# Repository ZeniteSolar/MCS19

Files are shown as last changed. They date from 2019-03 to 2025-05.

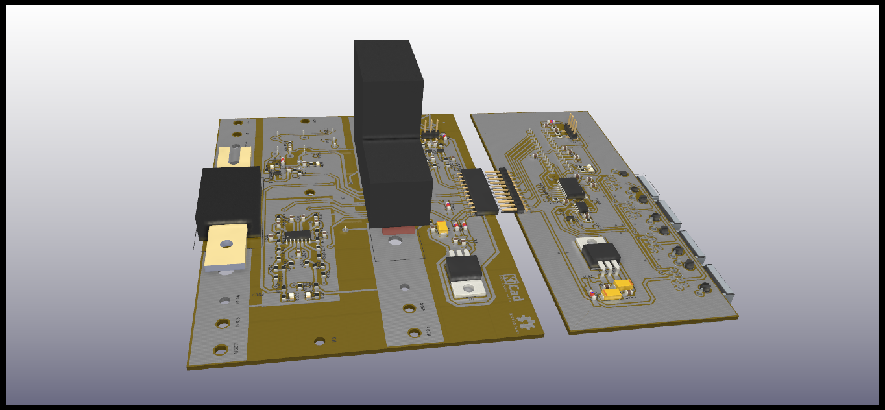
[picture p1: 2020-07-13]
hardware/IMG/3DUP.png

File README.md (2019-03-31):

# MCS19
**M**ódulo de **C**arregamento do **S**istema 2019  
Embarcação Guarapuvu II  
Equipe Zênite Solar  

### Sobre

Este módulo é responsável por gerenciar o carregamento do sistema com a finalidade de garantir segurança para a embarcação.

#### Requisitos e Abordagens
1. Gerenciar a conexão elétrica entre as baterias e o restante do sistema.
    - Utilizar de um relé de alta potência.
    - Ser controlado através da rede CAN da embarcação.
2. Proteger o sistema de falhas por sobre-corrente.
    - Utilizar de um fusível corretamente dimensionado.
3. Realizar o carregamento do banco de capacitores de maneira segura.
    - Utilização de um circuito de inrush.
        - Utilizar de um NTC para limitar o di/dt.
        - Utilizar de um resistor para limitar o pico de corrente
        - Utilizar de um relé para garantir a desconexão completa entre o sistema
      e o banco de baterias.
4. Facilitar o diagnóstico
    - Utilizar reportagens pela rede CAN
    - Utilizar LEDs e Buzzer
        - Sinalizar o estado dos relés
            - Relé do inrush
            - Relé principal
        - Sinalizar o estado do fusível principal
5. Garantir fixação mecânica que não flexione a PCB
    - Utilizar estrutura auxiliar de material isolante

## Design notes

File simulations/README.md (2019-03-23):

# Simulations
Software: LTSPICE

Arquivo: system_inrush.asc  
Descrição: simulação para validar considerando a topologia geral do sistema

Arquivo: ntc_inrush_temp_and_tol_variation.asc  
Descrição: simulação para validar o ntc considerando as tolerância e difernetes
temperaturas ambiente.

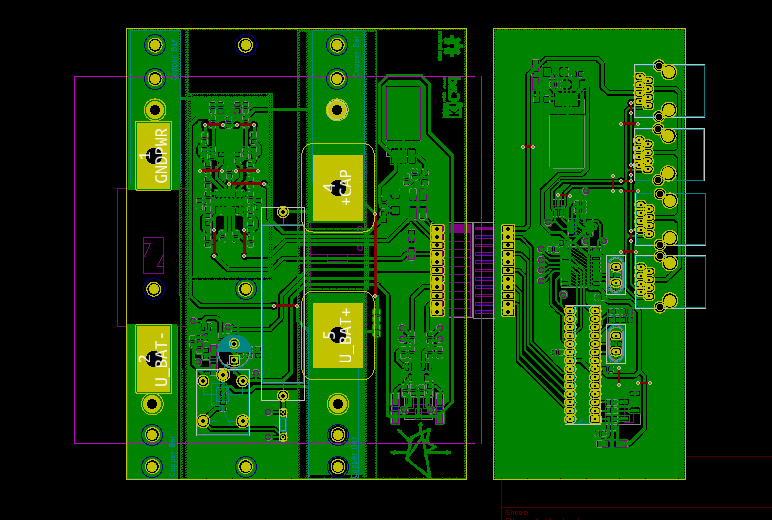
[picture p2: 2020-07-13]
hardware/IMG/layout.png

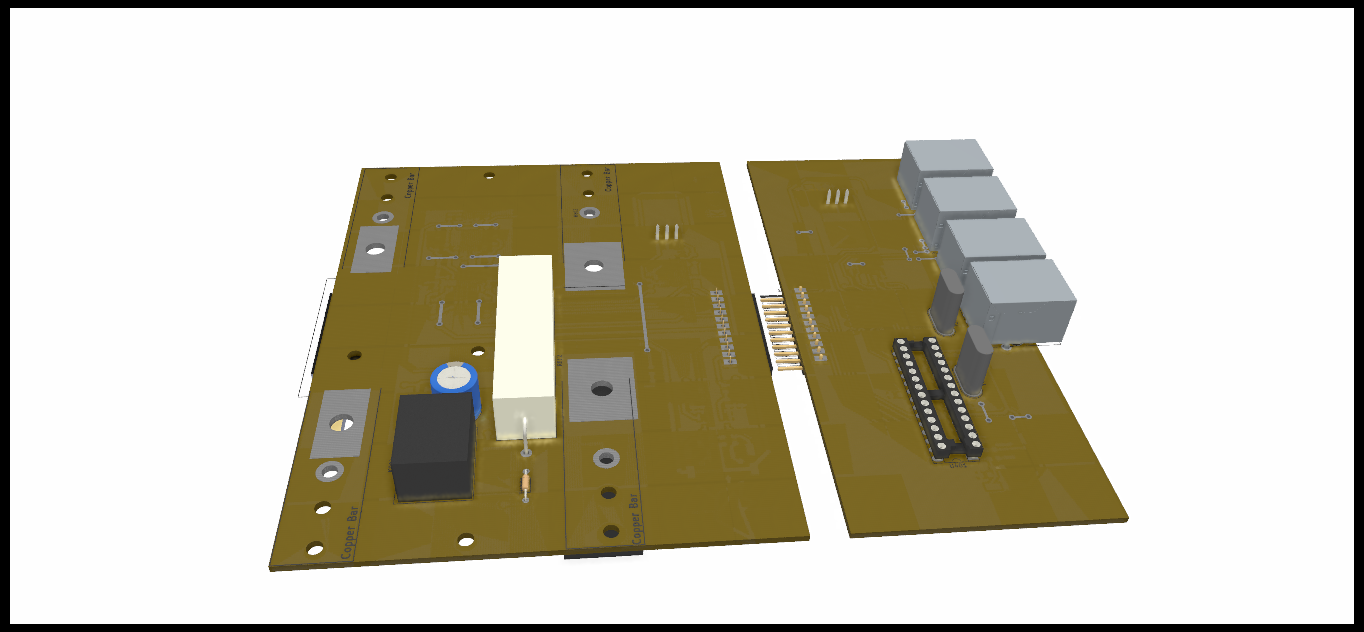
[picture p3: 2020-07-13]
hardware/IMG/3DDOWN.png

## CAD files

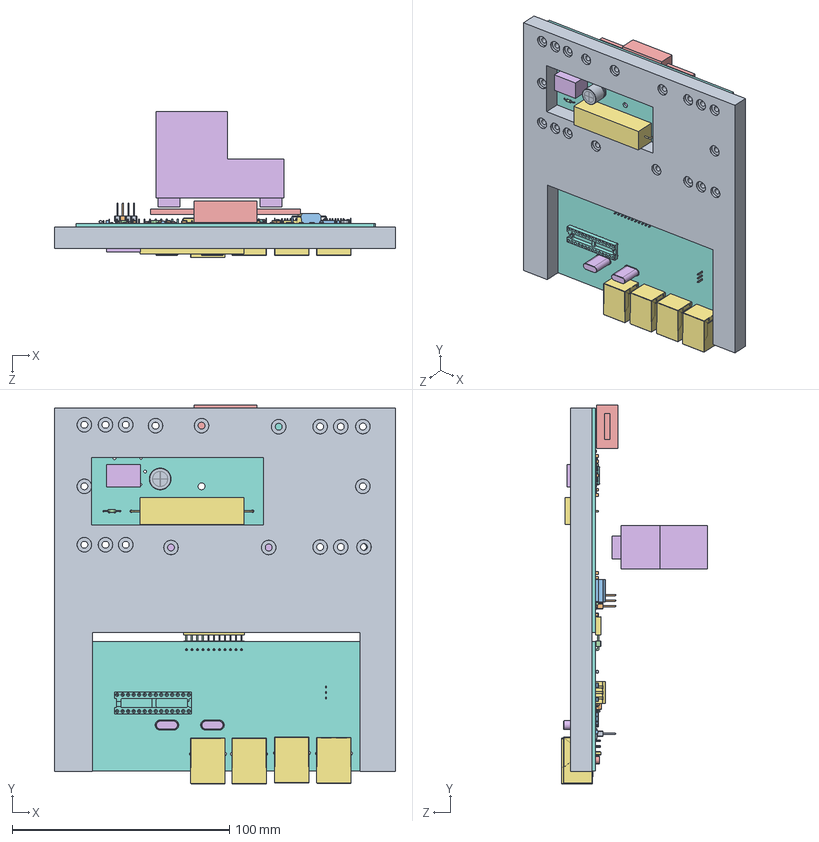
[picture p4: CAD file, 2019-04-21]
hardware/3D/assem/Assem85.SLDASM
157.2 x 174.6 x 67.5 mm
Part30^Assem85

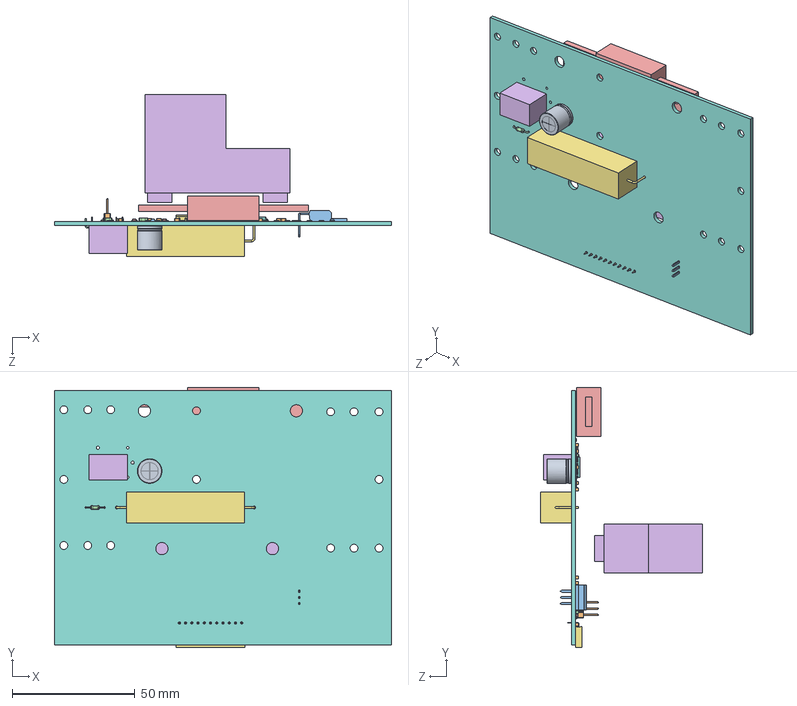
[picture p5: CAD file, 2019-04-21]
hardware/3D/charger/charger.SLDASM
137.2 x 105.9 x 65.8 mm

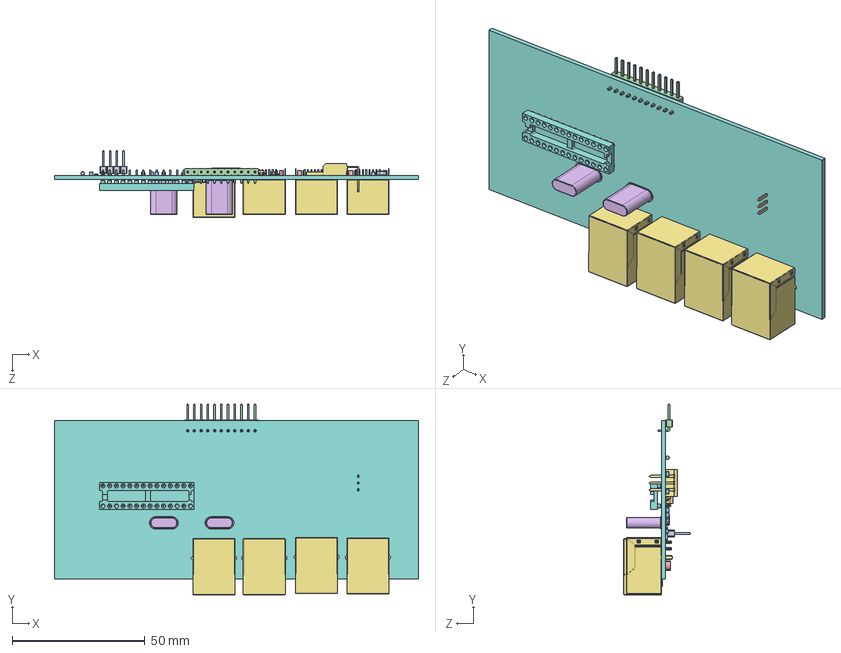
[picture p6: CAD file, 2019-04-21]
hardware/3D/control/control.SLDASM
137.2 x 71.9 x 25.1 mm

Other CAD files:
hardware/3D/control/TO-220-3_Horizontal_TabDown_1.sldasm
hardware/3D/control/PinHeader_1x04_P2.54mm_Vertical_SMD_Pin1Left.sldasm
hardware/3D/charger/LED_0805_2012Metric.sldasm
hardware/3D/charger/PinSocket_1x11_P2.54mm_Horizontal.sldasm
hardware/3D/charger/TSOT-23.sldasm
hardware/3D/assem/Assem1.SLDASM
hardware/3D/charger/D_MiniMELF.sldasm
hardware/3D/control/PinHeader_1x11_P2.54mm_Horizontal.sldasm
hardware/3D/control/R_0805_2012Metric_1.sldasm
hardware/3D/control/rj45.sldasm
hardware/3D/charger/R_Axial_Power_L48.0mm_W12.5mm_P55.88mm.sldasm
hardware/3D/control/SOIC-8_3.9x4.9mm_P1.27mm.sldasm
hardware/3D/charger/C_0805_2012Metric.sldasm
hardware/3D/control/Crystal_HC49-U_Vertical.sldasm
hardware/3D/charger/Fuse.sldasm
hardware/3D/assem/COMPOUND_1.sldprt
hardware/3D/assem/SOLID_1.sldprt
hardware/3D/assem/SOLID_1_10.sldprt
hardware/3D/assem/SOLID_1_11.sldprt
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

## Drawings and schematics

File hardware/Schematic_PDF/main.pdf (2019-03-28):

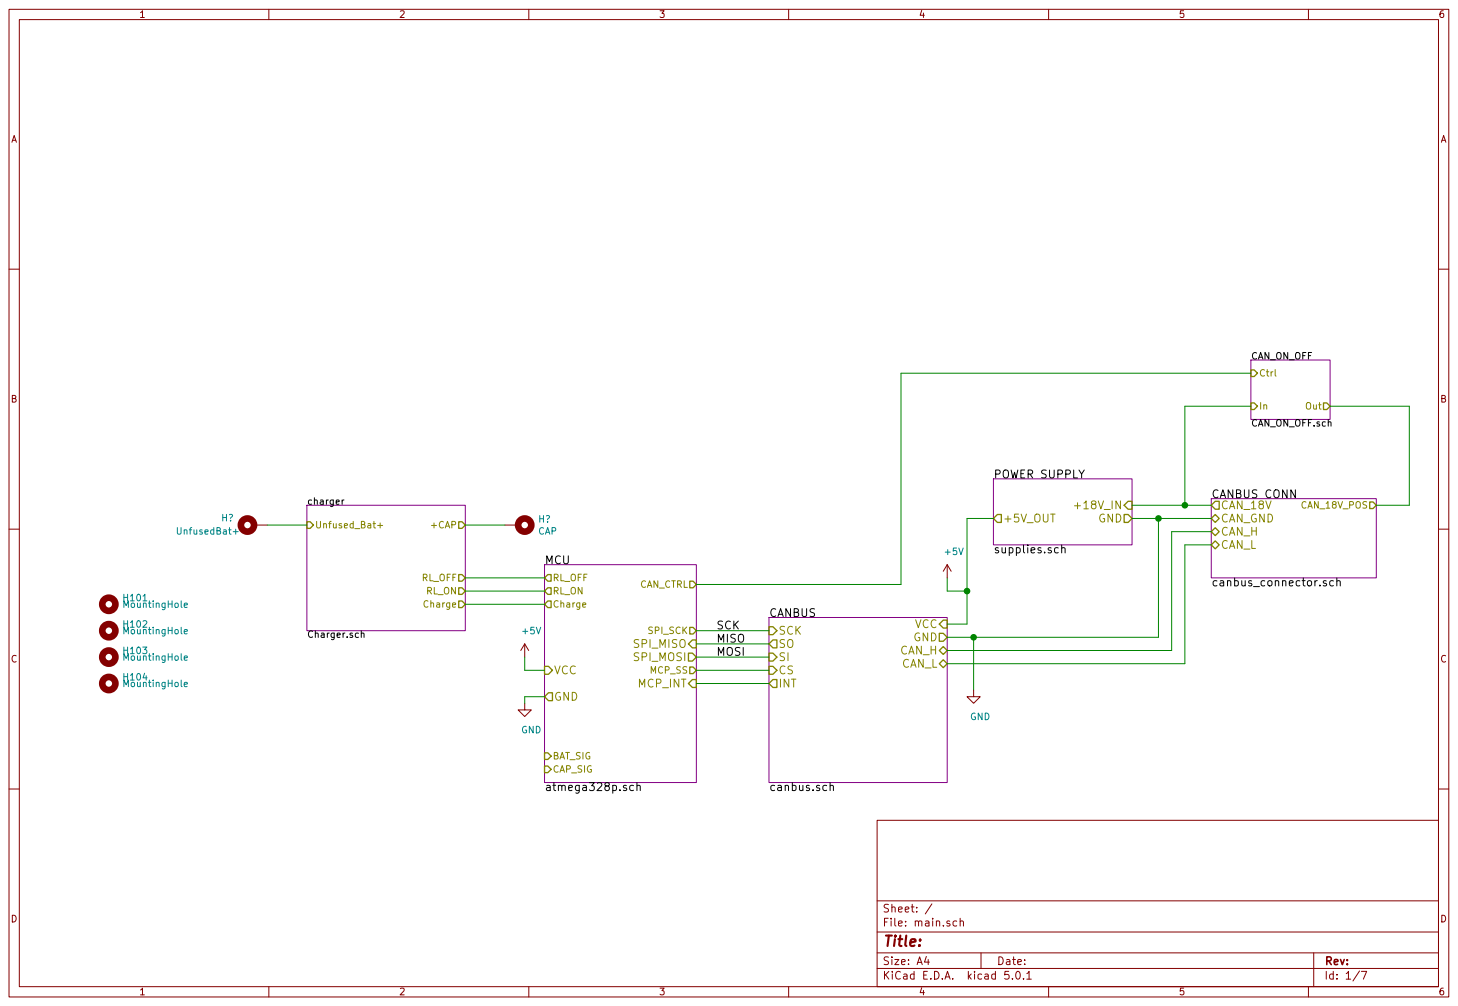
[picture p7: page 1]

Id: 1/7 Title: File: main.sch Sheet: / CANBUS
SCK
canbus.sch SI

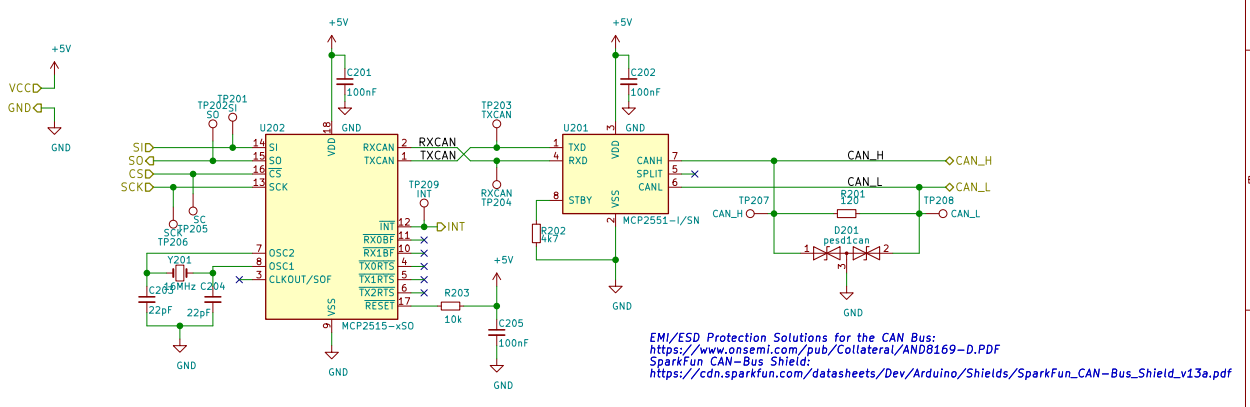
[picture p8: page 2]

https://cdn.sparkfun.com/datasheets/Dev/Arduino/Shields/SparkFun_CAN-Bus_Shield_v13a.pdf TP203 TXCAN

9 U202 MCP2515-xSO EMI/ESD Protection Solutions for the CAN Bus:

3 RXD 4 SPLIT 5 CANL 6 CANH 7 STBY 8 U201 MCP2551-I/SN TXCAN
RXCAN

EMI/ESD Protection Solutions for the CAN Bus:
https://www.onsemi.com/pub/Collateral/AND8169-D.PDF
SparkFun CAN-Bus Shield:
https://cdn.sparkfun.com/datasheets/Dev/Arduino/Shields/SparkFun_CAN-Bus_Shield_v13a.pdf

Id: 2/7 Title: File: canbus.sch Sheet: /CANBUS/

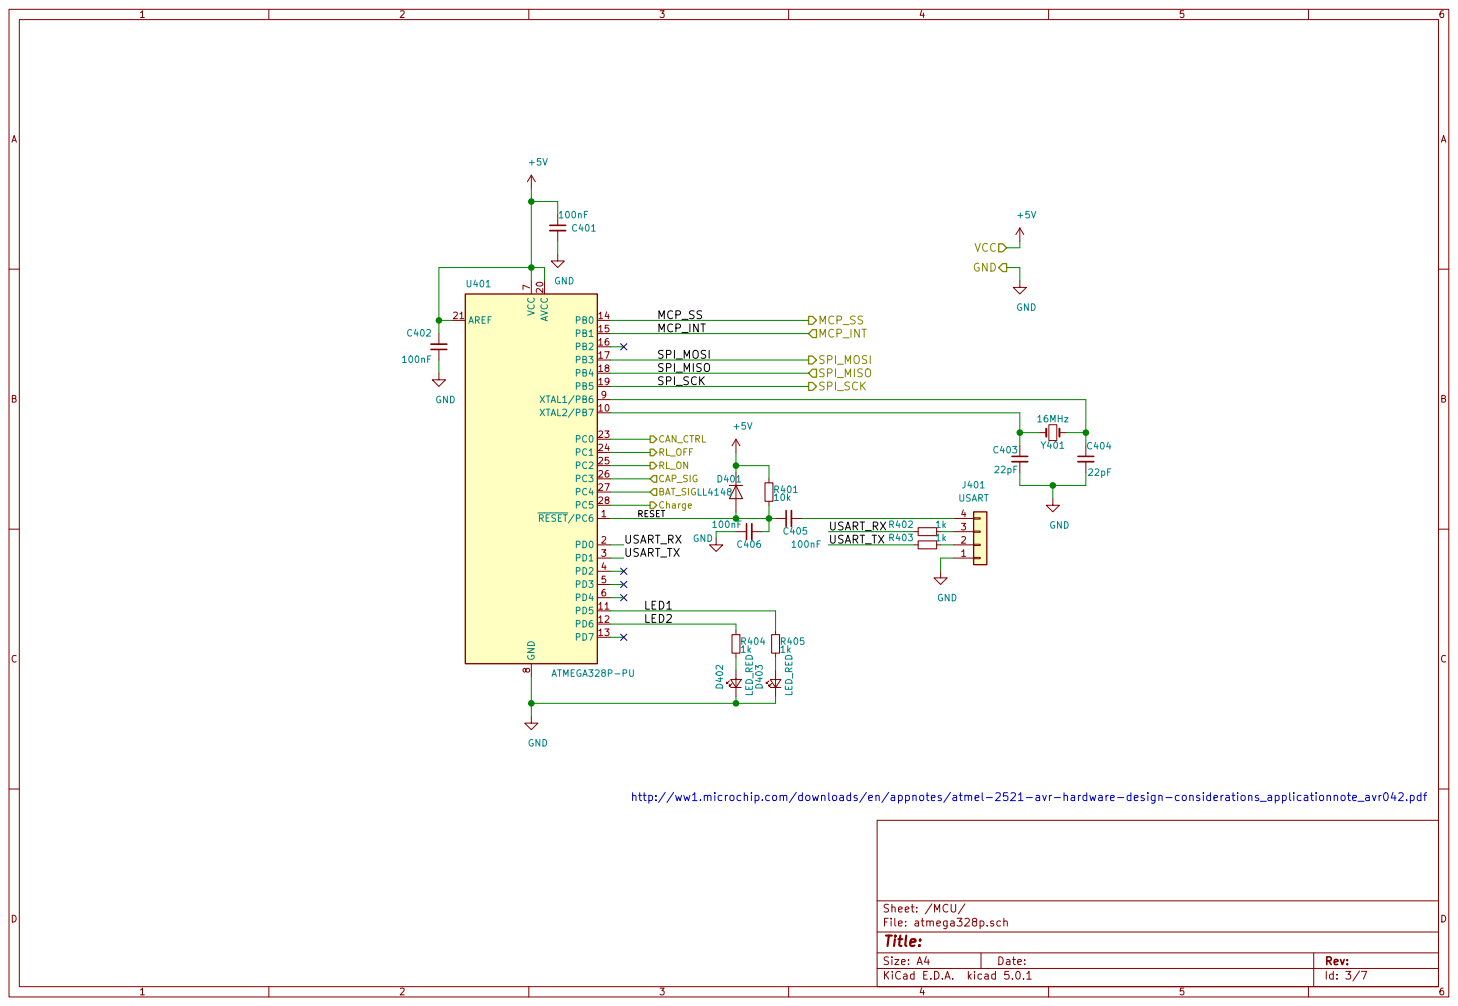
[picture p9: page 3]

File: atmega328p.sch Sheet: /MCU/
Id: 3/7 Title:

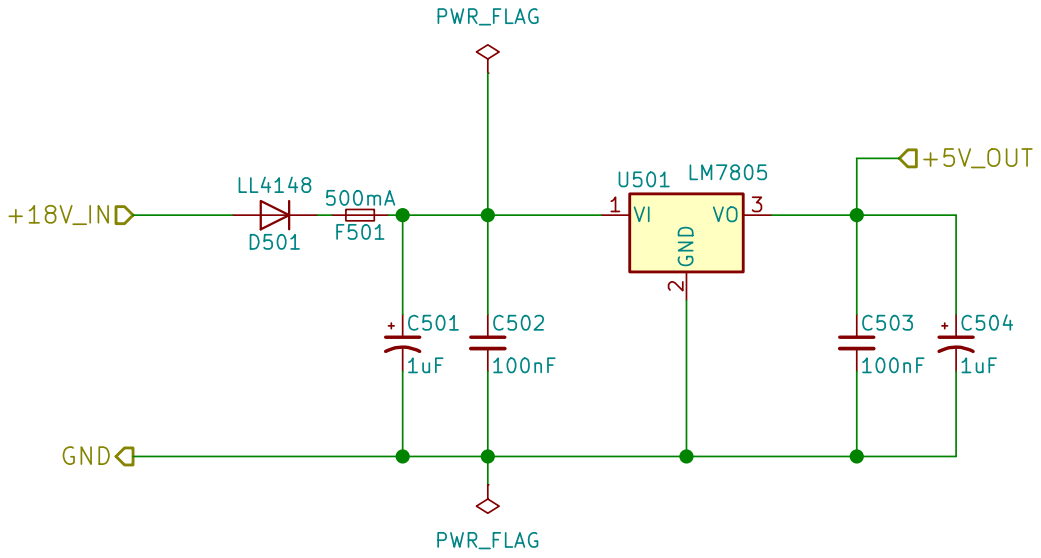
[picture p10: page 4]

File: supplies.sch Sheet: /POWER SUPPLY/
Id: 4/7 Title:

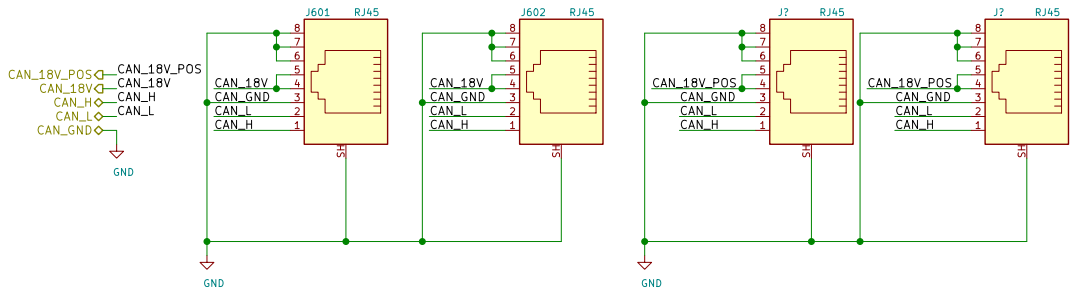
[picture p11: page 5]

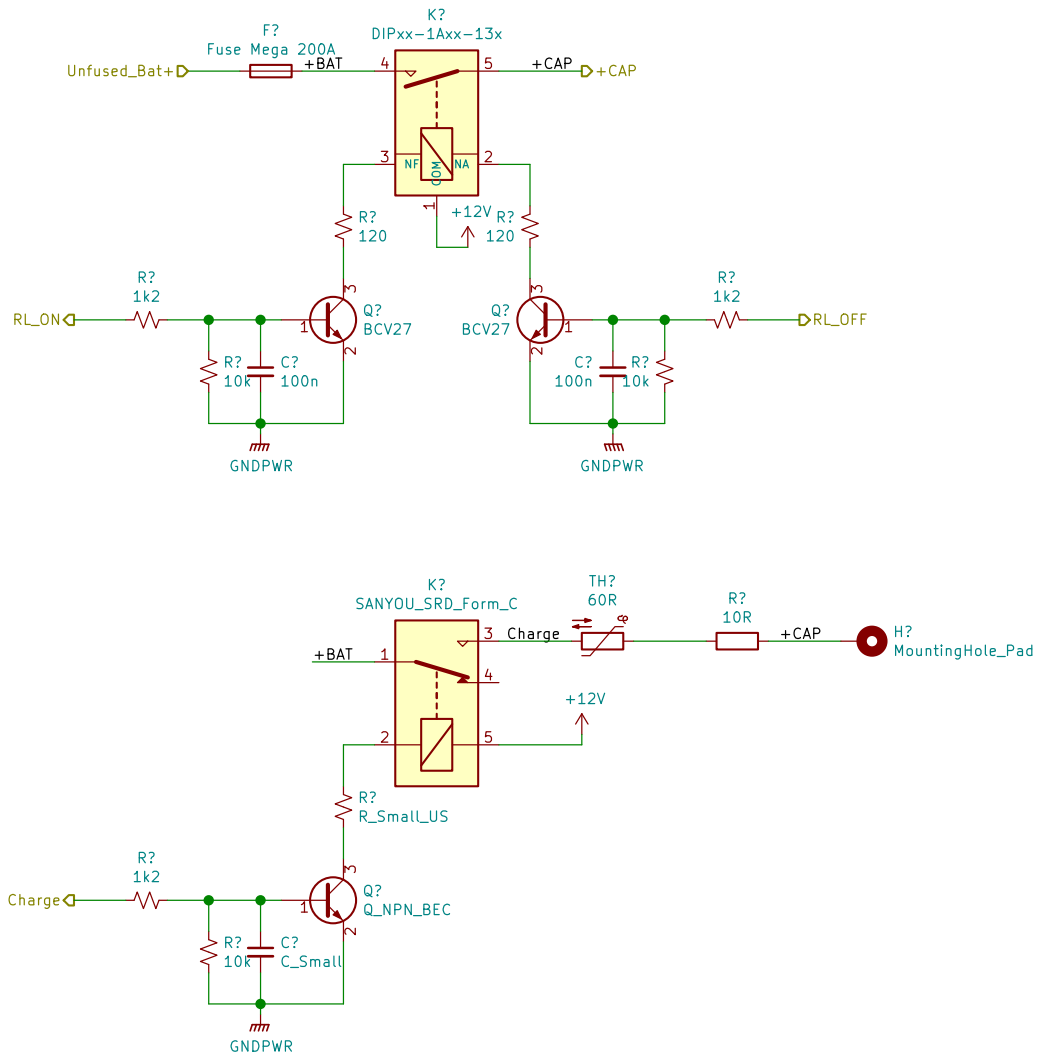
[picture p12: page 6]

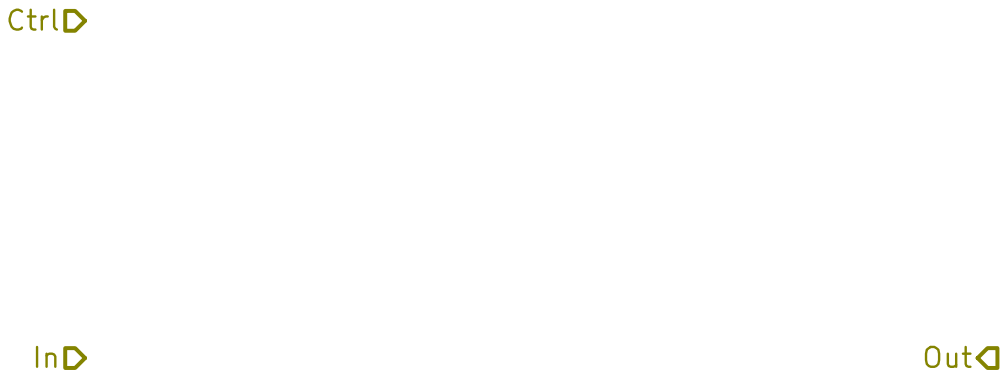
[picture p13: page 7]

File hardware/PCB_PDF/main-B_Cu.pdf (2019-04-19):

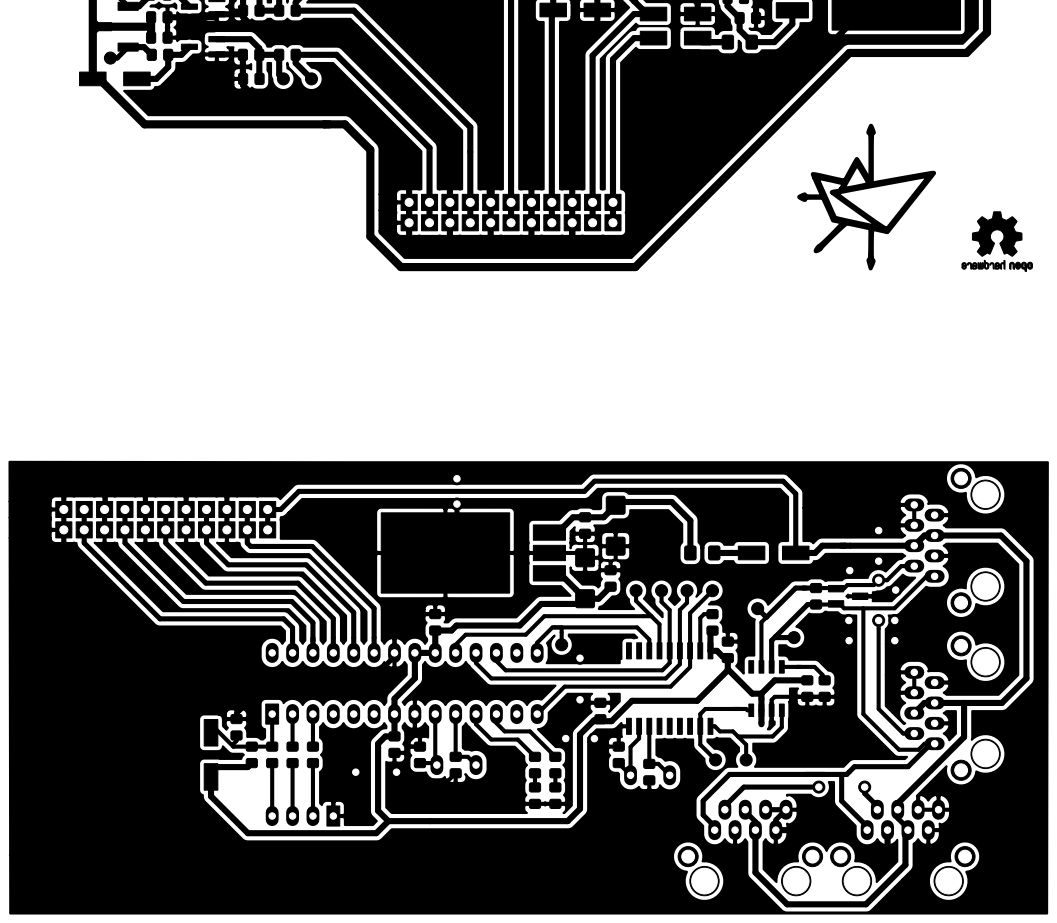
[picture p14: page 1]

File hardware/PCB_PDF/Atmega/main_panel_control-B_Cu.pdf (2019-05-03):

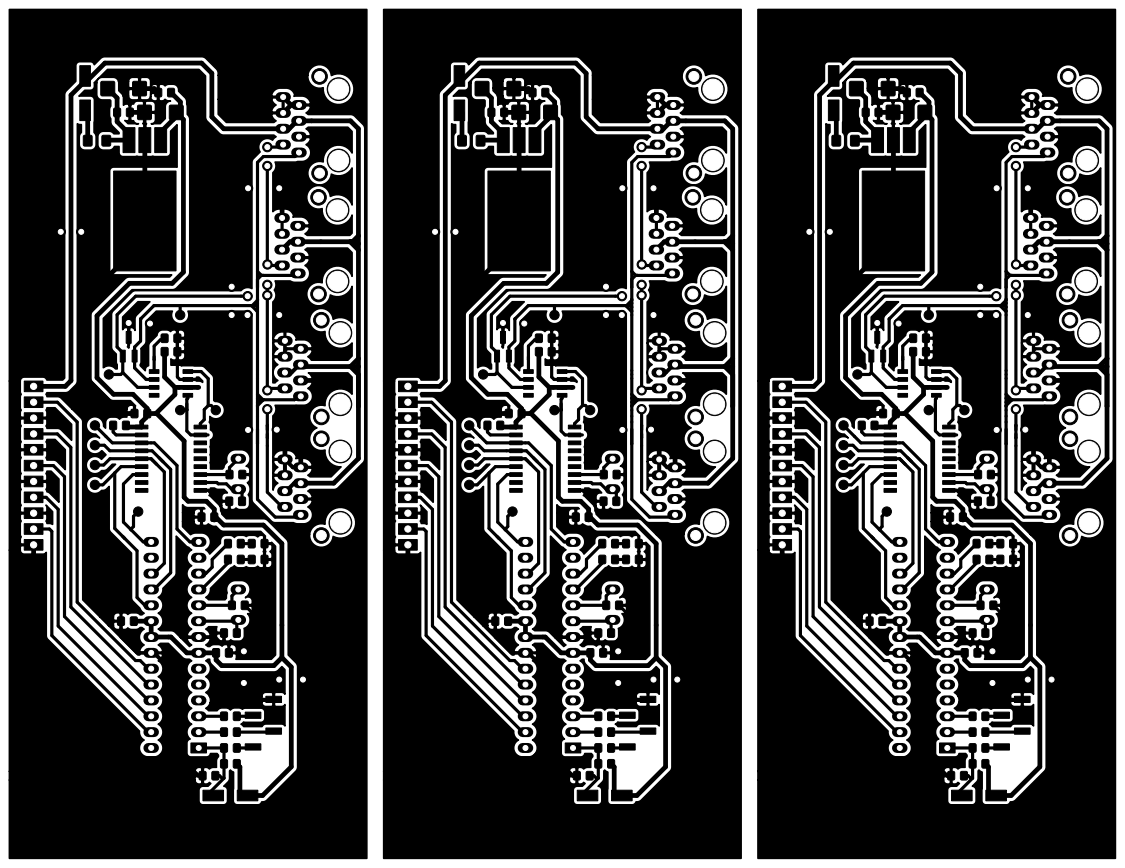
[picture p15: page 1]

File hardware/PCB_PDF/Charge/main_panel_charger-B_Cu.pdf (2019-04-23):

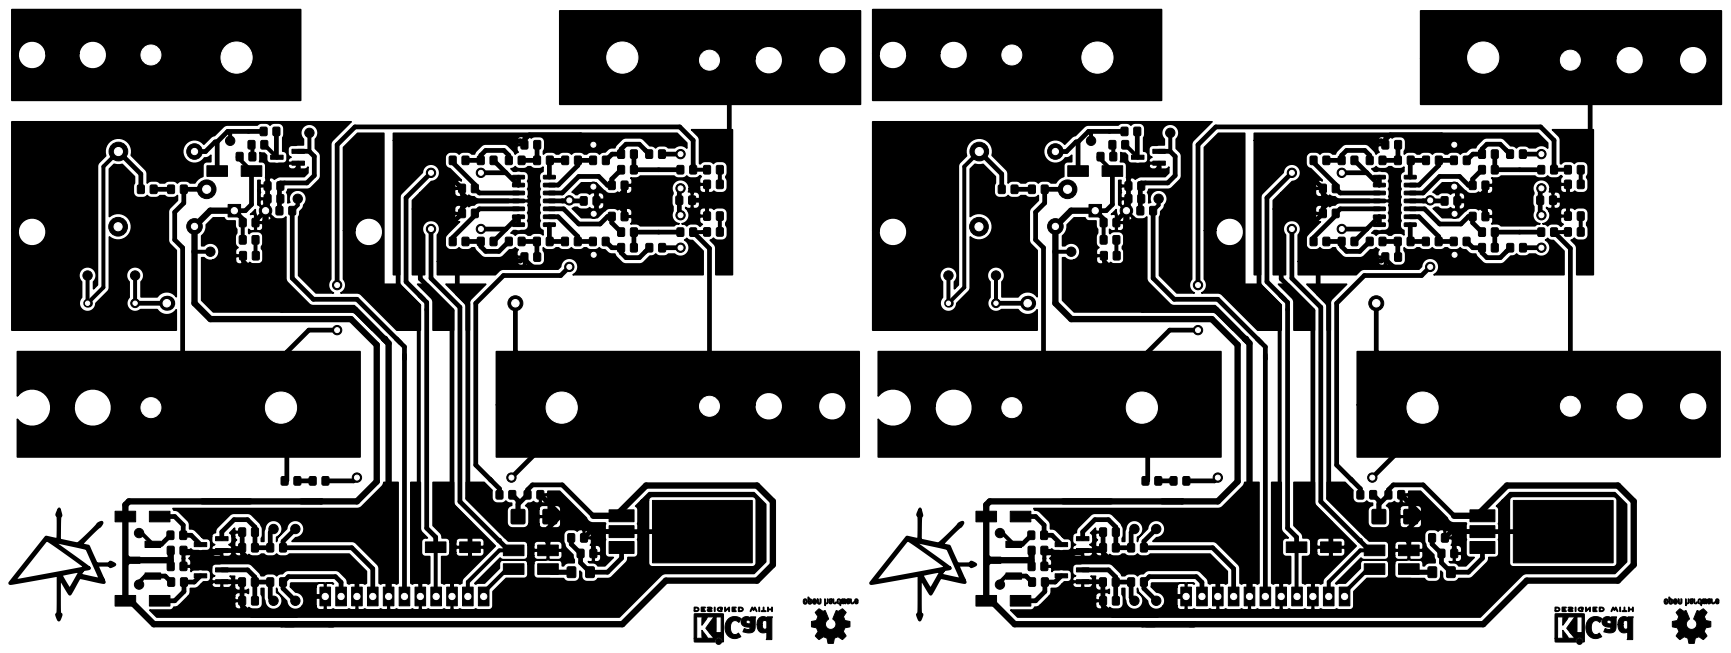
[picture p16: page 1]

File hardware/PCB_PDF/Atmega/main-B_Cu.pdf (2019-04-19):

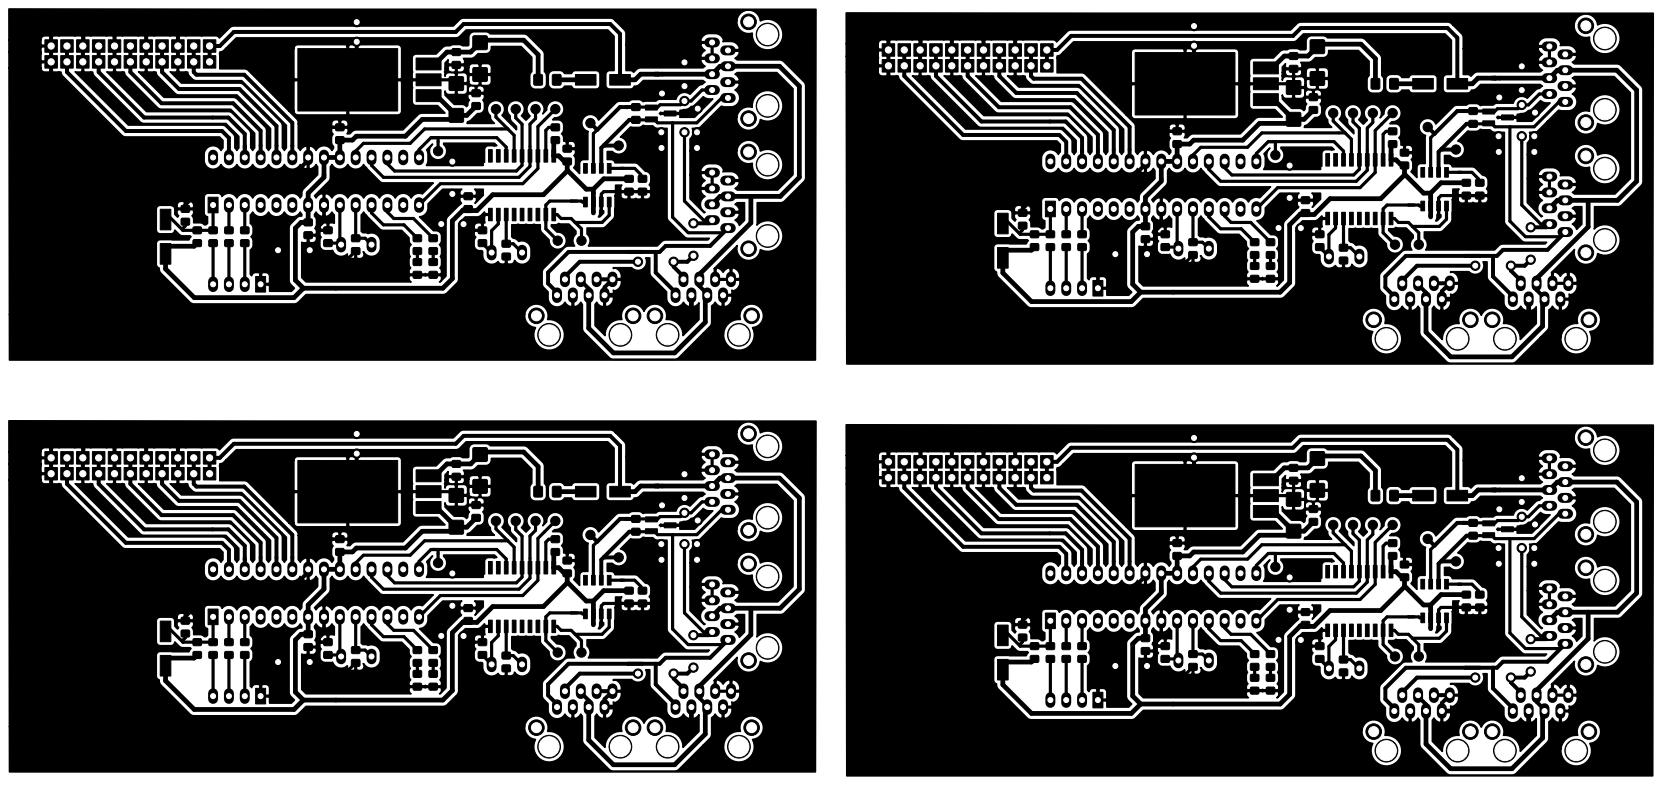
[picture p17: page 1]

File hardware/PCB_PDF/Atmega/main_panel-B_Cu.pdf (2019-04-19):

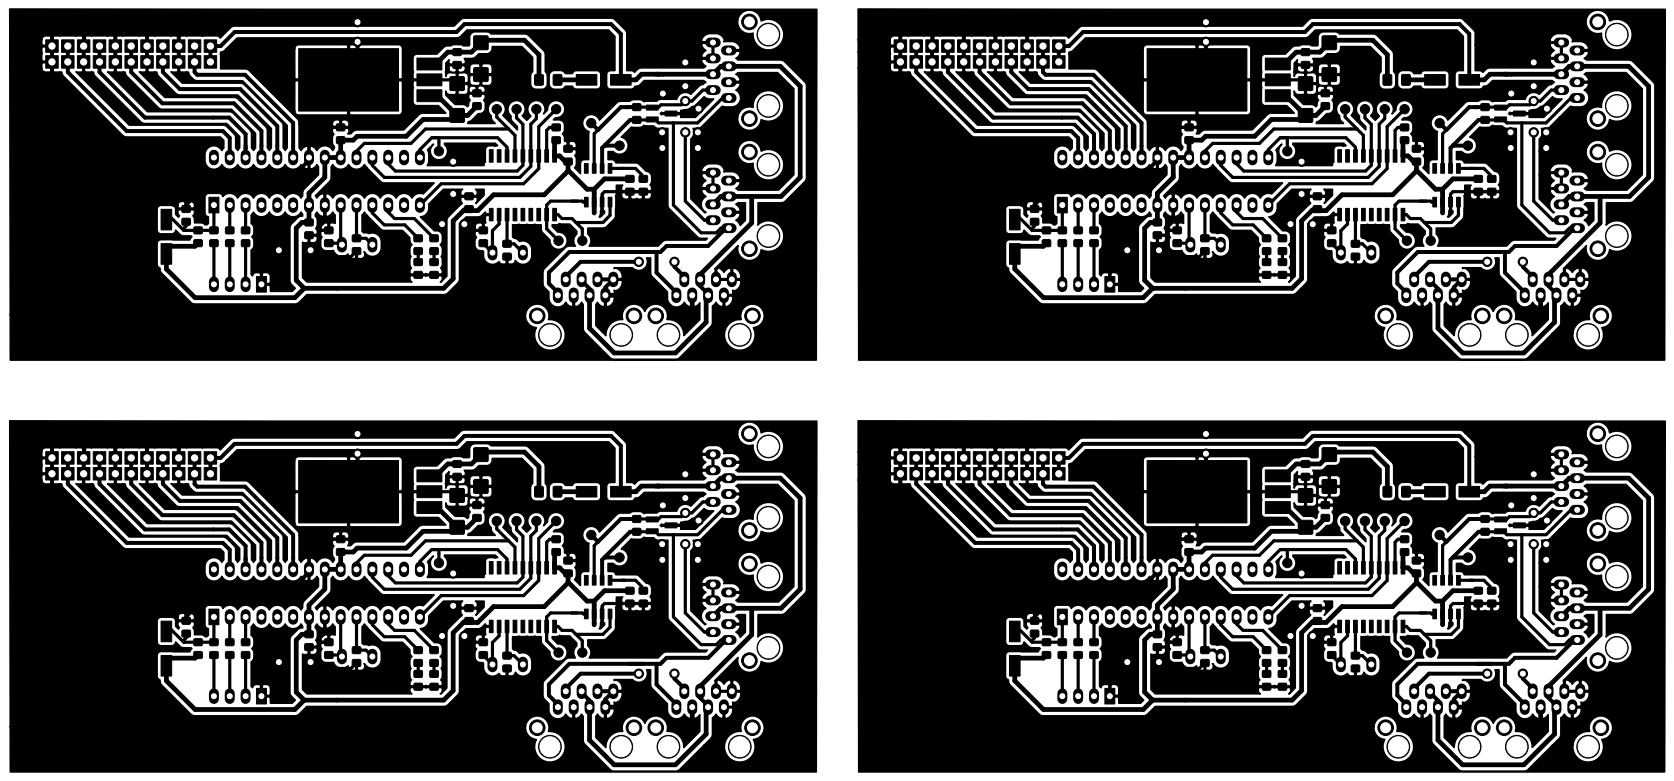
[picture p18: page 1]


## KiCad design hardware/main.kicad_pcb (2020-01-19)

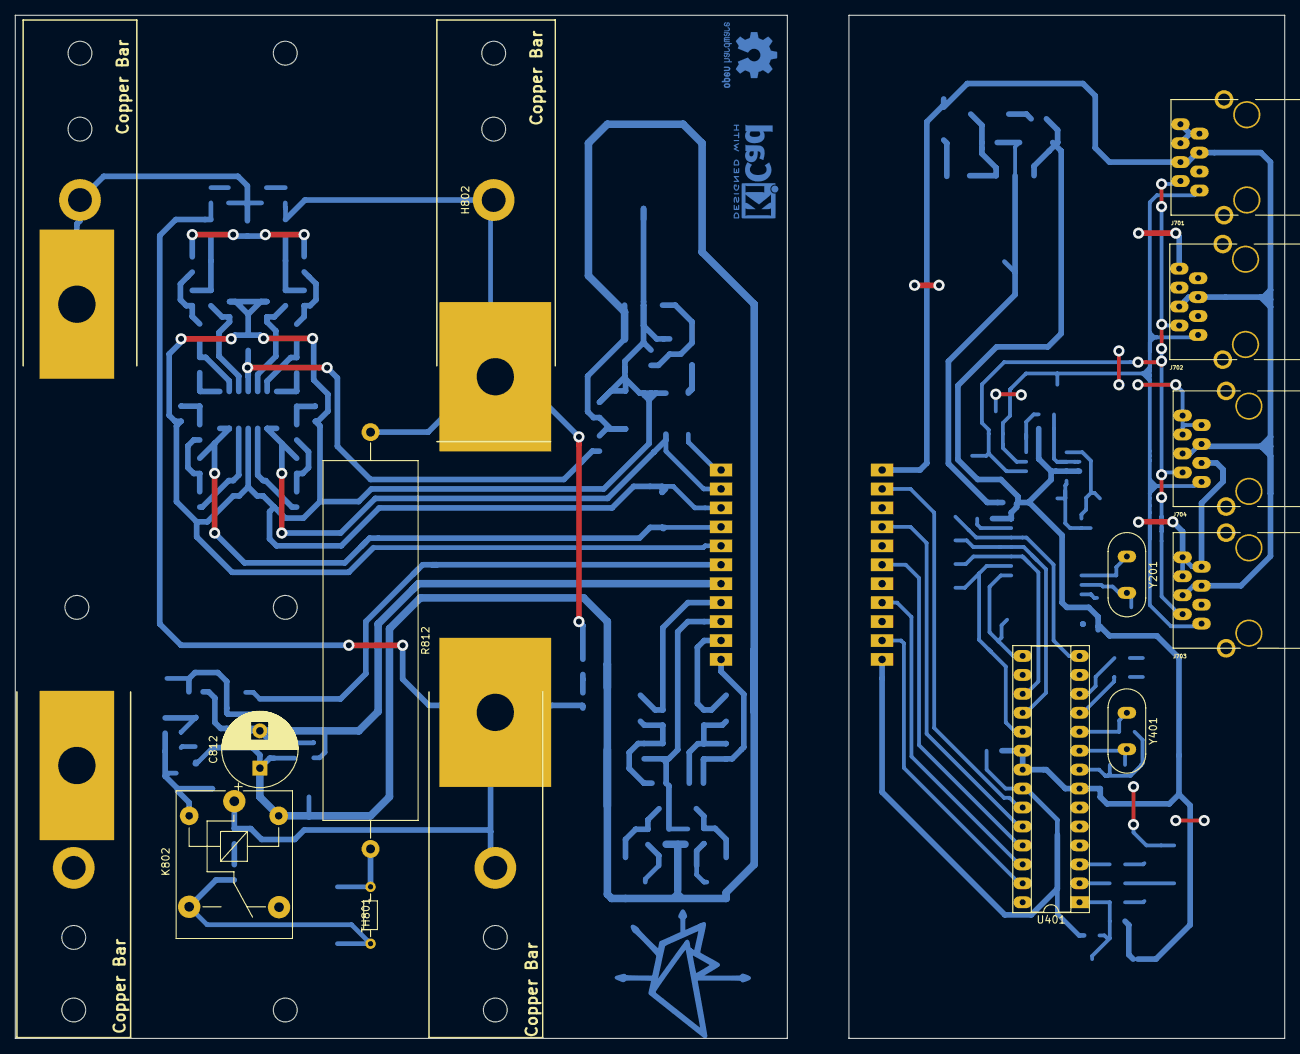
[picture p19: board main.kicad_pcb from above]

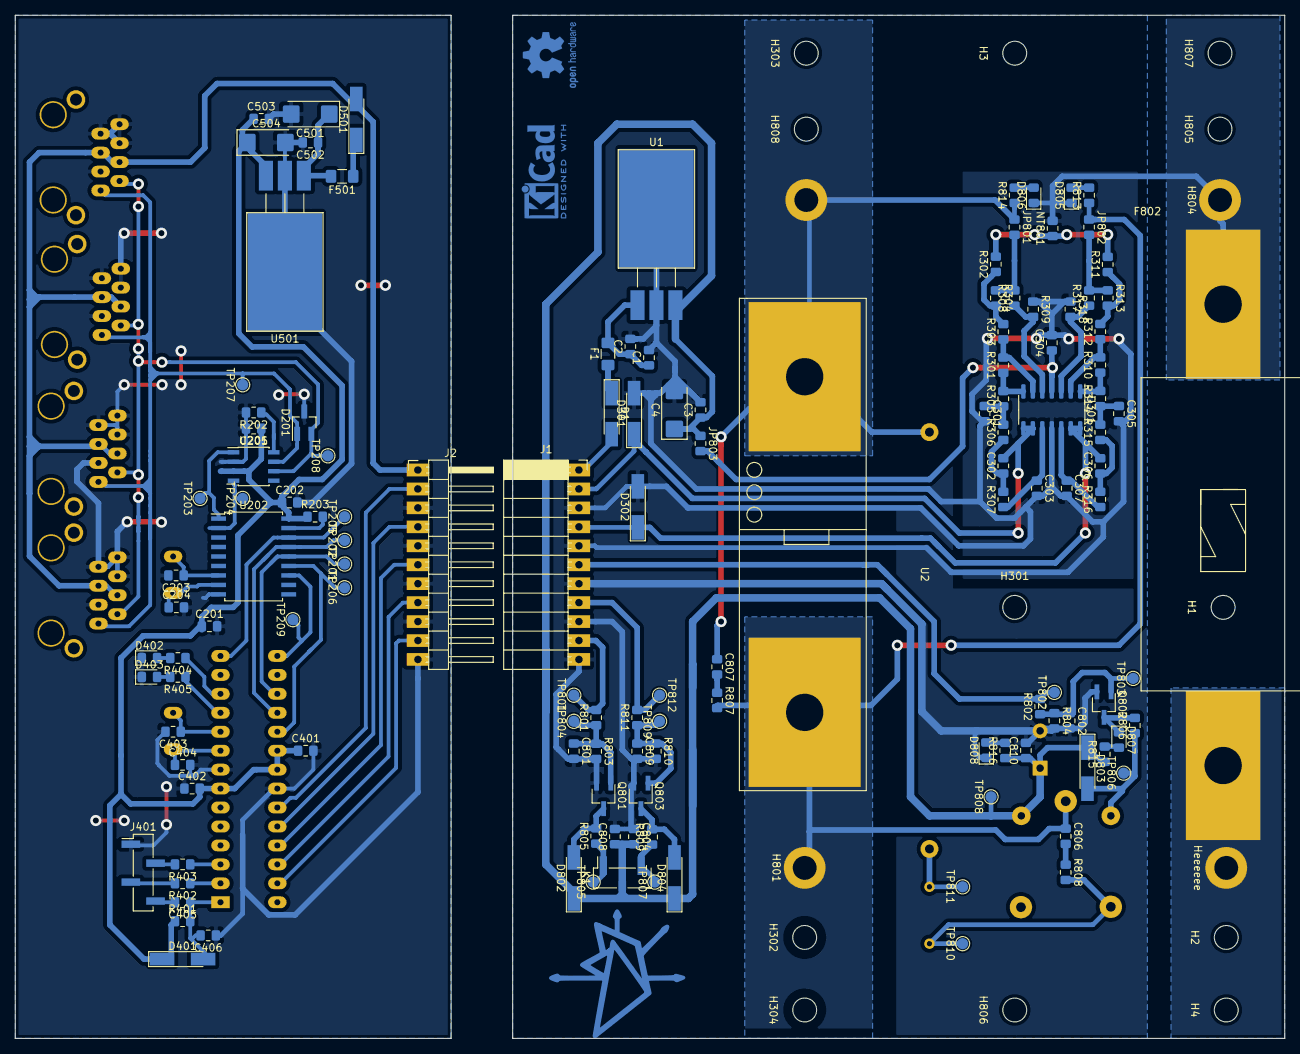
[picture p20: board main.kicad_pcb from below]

Board: 2 copper layers, 170.2 x 137.2 mm, 160 parts (147 on the bottom side), 83 nets.

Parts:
C1: 1uF; C_0805_2012Metric_Pad1.15x1.40mm_HandSolder
C2, C3, C201, C202, C205, C401, C402, C405, C406, C502, C503: 100nF; C_0805_2012Metric_Pad1.15x1.40mm_HandSolder
C4, C501, C504: 1uF; CP_EIA-6032-20_AVX-F_Pad2.25x2.35mm_HandSolder
C203, C204, C403, C404: 22pF; C_0805_2012Metric_Pad1.15x1.40mm_HandSolder
C301, C302, C303, C304, C305, C306, C307, C801, C802, C804, C806, C807, C808, C809, C810: 100n; C_0805_2012Metric_Pad1.15x1.40mm_HandSolder
C812: 4700u; CP_Radial_D10.0mm_P5.00mm
D1, D401, D501, D802, D803, D804: LL4148; D_MiniMELF_Handsoldering
D201: pesd1can; SOT-23_Handsoldering
D301, D302: 4V7; D_MiniMELF_Handsoldering
D402, D403: LED_RED; LED_0805_2012Metric_Pad1.15x1.40mm_HandSolder
D805: RED_LED; LED_0805_2012Metric_Pad1.15x1.40mm_HandSolder
D806, D808: GRN_LED; LED_0805_2012Metric_Pad1.15x1.40mm_HandSolder
D807: YLW_LED; LED_0805_2012Metric_Pad1.15x1.40mm_HandSolder
F1, F501: 500mA; Fuse_1206_3216Metric_Pad1.42x1.75mm_HandSolder
F802: Fuse Mega 200A; MegaFuse
H1, H2, H3, H4, H301, H302, H303, H304, H805, H806, H807, H808: MountingHole; MountingHole_3.2mm_M3
H801: U_BAT+; MountingHole_3.2mm_M3_DIN965_Pad
H802: +BAT; MountingHole_3.2mm_M3_DIN965_Pad
H804: F_BAT-; MountingHole_3.2mm_M3_DIN965_Pad
Heeeeee: U_BAT-; MountingHole_3.2mm_M3_DIN965_Pad
J1: Conn_01x11; PinSocket_1x11_P2.54mm_Horizontal
J2: Conn_01x11; PinHeader_1x11_P2.54mm_Horizontal
J401: USART; PinHeader_1x04_P2.54mm_Vertical_SMD_Pin1Left
J701, J702, J703, J704: 8P8C_Shielded; RJ45_YH59_01
JP801, JP802, JP803: Jp_TEST; R_0805_2012Metric_Pad1.15x1.40mm_HandSolder
K1: K100A; PinHeader_1x03_P2.54mm_Vertical_SMD_Pin1Right
K802: SANYOU_SRD_Form_C; Relay_SPDT_SANYOU_SRD_Series_Form_C
LOGO1: Logo_Open_Hardware_Small; zenite
LOGO2: Logo_Open_Hardware_Small; OSHW-Logo2_9.8x8mm_Copper
LOGO3: Logo_Open_Hardware_Small; KiCad-Logo2_5mm_Copper
NT801: Net-Tie_2; R_0805_2012Metric_Pad1.15x1.40mm_HandSolder
Q801, Q803: BCV27; TSOT-23_HandSoldering
Q802: Q_NPN_BEC; TSOT-23_HandSoldering
R202: 4k7; R_0805_2012Metric_Pad1.15x1.40mm_HandSolder
R203, R301, R303, R304, R308, R309, R310, R312, R313, R317, R318, R401, R803, R804, R810: 10k; R_0805_2012Metric_Pad1.15x1.40mm_HandSolder
R302, R311: 100k; R_0805_2012Metric_Pad1.15x1.40mm_HandSolder
R305, R306, R307, R314, R315, R316, R402, R403, R404, R405: 1k; R_0805_2012Metric_Pad1.15x1.40mm_HandSolder
R801, R802, R811: 1k2; R_0805_2012Metric_Pad1.15x1.40mm_HandSolder
R805, R806, R809: 120; R_0805_2012Metric_Pad1.15x1.40mm_HandSolder
R807, R808: 1R; R_0805_2012Metric_Pad1.15x1.40mm_HandSolder
R812: 10R; R_Axial_Power_L48.0mm_W12.5mm_P55.88mm
R813, R814: 2k5; R_0805_2012Metric_Pad1.15x1.40mm_HandSolder
R815, R816: 470; R_0805_2012Metric_Pad1.15x1.40mm_HandSolder
TH801: 60R; R_Axial_DIN0204_L3.6mm_D1.6mm_P7.62mm_Horizontal
TP201: SI; TestPoint_Pad_D1.5mm
TP202: SO; TestPoint_Pad_D1.5mm
TP203: TXCAN; TestPoint_Pad_D1.5mm
TP204: RXCAN; TestPoint_Pad_D1.5mm
TP205: SC; TestPoint_Pad_D1.5mm
TP206: SCK; TestPoint_Pad_D1.5mm
TP207: CAN_H; TestPoint_Pad_D1.5mm
TP208: CAN_L; TestPoint_Pad_D1.5mm
TP209: INT; TestPoint_Pad_D1.5mm
TP801: RL_ON; TestPoint_Pad_D1.5mm
TP802: Charge; TestPoint_Pad_D1.5mm
TP803: B_CH; TestPoint_Pad_D1.5mm
TP804: B_ON; TestPoint_Pad_D1.5mm
TP805: ON; TestPoint_Pad_D1.5mm
TP806: CH-; TestPoint_Pad_D1.5mm
TP807: OFF; TestPoint_Pad_D1.5mm
TP808: CH+; TestPoint_Pad_D1.5mm
TP809: B_OFF; TestPoint_Pad_D1.5mm
TP810: TH+; TestPoint_Pad_D1.5mm
TP811: TH-; TestPoint_Pad_D1.5mm
TP812: RL_OFF; TestPoint_Pad_D1.5mm
U1: LM7812; TO-220-3_Horizontal_TabDown_SMD
U2: K100B; Mega_Relay_K100_separated
U201: MCP2551-I/SN; SOIC-8_3.9x4.9mm_P1.27mm
U202: MCP2515-xSO; SOIC-18W_7.5x11.6mm_P1.27mm
U301: LM324; SOIC-14_3.9x8.7mm_P1.27mm
U401: ATMEGA328P-PU; DIP-28_W7.62mm_Socket
U501: LM7805; TO-220-3_Horizontal_TabDown_SMD
Y201, Y401: 16MHz; Crystal_HC49-U_Vertical

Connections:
+5V: C201.1, C202.1, C205.1, C401.1, C402.2, C503.1, C504.1, D401.1, R203.1, R401.1, U201.3, U202.18, U401.7, U401.20, U401.21, U501.3
+12VA: C304.1, JP803.2, U301.4
/CHARGER/+12V: C3.1, C4.1, C804.2, C808.1, C810.1, C812.1, D802.1, D803.1, D804.1, JP803.1, K1.2, K802.5, R815.1, R816.1, TP808.1, U1.3
/CHARGER/+18V_IN: D1.2, J1.1
/CHARGER/+CAP: C807.1, H802.1, JP801.1, R812.1, R814.1, U2.4
/CHARGER/CH: K802.3, R808.2, TH801.2......, TP810.1
/CHARGER/Charge: J1.6, R802.2, TP802.1
/CHARGER/RL_OFF: J1.8, R811.2, TP812.1
/CHARGER/RL_ON: J1.10, R801.2, TP801.1
/CHARGER/S_RL_ON: D807.1, Q802.3, R806.2
/CHARGER/U_BAT+: C806.1, H801.1, JP802.1, K802.1, R807.2, R813.1, U2.5
/CHARGER/U_BAT-: F802.2, Heeeeee.1
/CHARGER/sheet5CBAED96/in1+: JP801.2, R304.1, R308.2
/CHARGER/sheet5CBAED96/in2+: JP802.2, R313.1, R317.2
/CHARGER/sig_bat+: C306.2, D302.1, J1.4, U301.13, U301.14
/CHARGER/sig_cap+: C302.2, D301.1, J1.2, U301.8, U301.9
/CONTROLLER/+18V_OUT: D501.2, J2.1, J701.4, J701.5, J702.4, J702.5, J703.4, J703.5, J704.4, J704.5
/CONTROLLER/Charge: J2.6, U401.25
/CONTROLLER/MISO: TP202.1, U202.15, U401.18
/CONTROLLER/MOSI: TP201.1, U202.14, U401.17
/CONTROLLER/RL_OFF: J2.8, U401.26
/CONTROLLER/RL_ON: J2.10, U401.27
/CONTROLLER/SCK: TP206.1, U202.13, U401.19
/CONTROLLER/sheet5CA5A59C/CAN_H: D201.1, J701.1, J702.1, J703.1, J704.1, TP207.1, U201.7
/CONTROLLER/sheet5CA5A59C/CAN_L: D201.2, J701.2, J702.2, J703.2, J704.2, TP208.1, U201.6
/CONTROLLER/sheet5CA5A59C/CS: TP205.1, U202.16, U401.14
/CONTROLLER/sheet5CA5A59C/INT: TP209.1, U202.12, U401.15
/CONTROLLER/sheet5CA5A59C/RXCAN: TP204.1, U201.4, U202.2
/CONTROLLER/sheet5CA5A59C/TXCAN: TP203.1, U201.1, U202.1
/CONTROLLER/sheet5CA5A59D/LED1: R405.1, U401.11
/CONTROLLER/sheet5CA5A59D/LED2: R404.1, U401.12
/CONTROLLER/sheet5CA5A59D/RESET: C405.1, C406.2, D401.2, R401.2, U401.1
/CONTROLLER/sheet5CA5A59D/USART_RX: R402.1, U401.2
/CONTROLLER/sheet5CA5A59D/USART_TX: R403.1, U401.3
/CONTROLLER/sig_bat+: J2.4, U401.24
/CONTROLLER/sig_cap+: J2.2, U401.23
GND: C201.2, C202.2, C203.2, C204.2, C205.2, C401.2, C402.1, C403.2, C404.2, C406.1, C501.2, C502.2, C503.2, C504.2, D201.3, D402.1, D403.1, J2.3, J2.5, J2.7, J2.9, J2.11, J401.1, J701.3, J701.6, J701.7, J701.8, J702.3, J702.6, J702.7, J702.8, J703.3, J703.6, J703.7, J703.8, J704.3, J704.6, J704.7, J704.8, R202.2, U201.2, U202.9, U401.8, U401.22, U501.2
GNDA: NT801.1, R302.2, R311.2
GNDPWR: C1.2, C2.2, C3.2, C4.2, C301.2, C303.2, C304.2, C305.2, C307.2, C801.2, C802.2, C804.1, C808.2, C809.2, C810.2, C812.2, D301.2, D302.2, D805.1, D806.1, D808.1, F802.1, H804.1, J1.3, J1.5, J1.7, J1.9, J1.11, NT801.2, Q801.2, Q802.2, Q803.2, R309.1, R318.1, R803.2, R804.2, R810.2, U1.2, U301.11
unnamed: C1.1, C2.1, F1.2, U1.1
unnamed: C203.1, U202.7, Y201.1
unnamed: C204.1, U202.8, Y201.2
unnamed: C301.1, R305.1, R306.2
unnamed: C302.1, R306.1, R307.2
unnamed: C303.1, R307.1, U301.10
unnamed: C305.1, R314.1, R315.2
unnamed: C306.1, R315.1, R316.2
unnamed: C307.1, R316.1, U301.12
unnamed: C403.1, U401.10, Y401.1
unnamed: C404.1, U401.9, Y401.2
unnamed: C405.2, J401.4
unnamed: C501.1, C502.1, F501.2, U501.1
unnamed: C801.1, Q801.1, R801.1, R803.1, TP804.1
unnamed: C802.1, Q802.1, R802.1, R804.1, TP803.1
unnamed: C806.2, R808.1
unnamed: C807.2, R807.1
unnamed: C809.1, Q803.1, R810.1, R811.1, TP809.1
unnamed: D1.1, F1.1
unnamed: D402.2, R404.2
unnamed: D403.2, R405.2
unnamed: D501.1, F501.1
unnamed: D802.2, Q801.3, R805.2
unnamed: D803.2, K802.2, R806.1, TP806.1
unnamed: D804.2, Q803.3, R809.2
unnamed: D805.2, R813.2
unnamed: D806.2, R814.2
unnamed: D807.2, R815.2
unnamed: D808.2, R816.2
unnamed: J401.2, R403.2
unnamed: J401.3, R402.2
unnamed: K1.1, R805.1, TP805.1
unnamed: K1.3, R809.1, TP807.1
unnamed: R202.1, U201.8
unnamed: R203.2, U202.17
unnamed: R301.1, R305.2, U301.7
unnamed: R301.2, R303.1, U301.6
unnamed: R302.1, R303.2, R304.2
unnamed: R308.1, R309.2, U301.5
unnamed: R310.1, R314.2, U301.1
unnamed: R310.2, R312.1, U301.2
unnamed: R311.1, R312.2, R313.2
unnamed: R317.1, R318.2, U301.3
unnamed: R812.2, TH801.1, TP811.1

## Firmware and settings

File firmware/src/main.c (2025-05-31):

// coding: utf-8

#include "main.h"

void init(void)
{

    #ifdef USART_ON
        usart_init(MYUBRR,1,1);                         // inicializa a usart
        VERBOSE_MSG_INIT(usart_send_string("\n\n\nUSART... OK!\n"));
    #endif

    _delay_ms(200);

    #ifdef WATCHDOG_ON
        VERBOSE_MSG_INIT(usart_send_string("WATCHDOG..."));
        wdt_init();
        VERBOSE_MSG_INIT(usart_send_string(" OK!\n"));
        wdt_reset();
    #else
        VERBOSE_MSG_INIT(usart_send_string("WATCHDOG... OFF!\n"));
    #endif

    #ifdef WATCHDOG_ON
        wdt_reset();
    #endif

    #ifdef SPI_ON
        set_bit(DDRB, PB2);     //output to be the spi master
    #endif

    #ifdef CAN_ON
        VERBOSE_MSG_INIT(usart_send_string("CAN (500kbps)..."));
        can_init(BITRATE_500_KBPS);
        //can_set_mode(LOOPBACK_MODE);
        VERBOSE_MSG_INIT(usart_send_string(" OK!\n"));
        VERBOSE_MSG_INIT(usart_send_string("CAN filters..."));
        can_static_filter(can_filter);
        VERBOSE_MSG_INIT(usart_send_string(" OK!\n"));
    #else
        VERBOSE_MSG_INIT(usart_send_string("CAN... OFF!\n"));
    #endif

    #ifdef WATCHDOG_ON
        wdt_reset();
    #endif

    #ifdef ADC_ON
        VERBOSE_MSG_INIT(usart_send_string("ADC..."));
        adc_init();
        VERBOSE_MSG_INIT(usart_send_string(" OK!\n"));
    #else
        VERBOSE_MSG_INIT(usart_send_string("ADC... OFF!\n"));
    #endif

    #ifdef WATCHDOG_ON
        wdt_reset();
    #endif

    #ifdef SLEEP_ON 
        VERBOSE_MSG_INIT(usart_send_string("SLEEP..."));
        sleep_init();
        VERBOSE_MSG_INIT(usart_send_string(" OK!\n"));
    #else
        VERBOSE_MSG_INIT(usart_send_string("SLEEP... OFF!\n"));
    #endif

    #ifdef WATCHDOG_ON
        wdt_reset();
    #endif

 	#ifdef MACHINE_ON
        VERBOSE_MSG_INIT(usart_send_string("MACHINE..."));
		machine_init();
        VERBOSE_MSG_INIT(usart_send_string(" OK!\n"));
    #else
        VERBOSE_MSG_INIT(usart_send_string("MACHINE... OFF!\n"));
	#endif

    #ifdef WATCHDOG_ON
        wdt_reset();
    #endif
	
    #ifdef LED_ON
        set_bit(LED_DDR, LED1);                      // LED como saída
        set_bit(LED_DDR, LED2);                      // LED como saída
        VERBOSE_MSG_INIT(usart_send_string("LED... OK!\n"));
    #else
        VERBOSE_MSG_INIT(usart_send_string("LED... OFF!\n"));
    #endif

    #ifdef WATCHDOG_ON
        wdt_reset();
    #endif

    #ifdef MACHINE_ON
        print_configurations();
    #endif // MACHINE_ON

    set_bit(MAINRELAY_DDR, MAINRELAY_ON);
    set_bit(MAINRELAY_DDR, MAINRELAY_OFF);
    set_bit(CHARGERELAY_DDR, CHARGERELAY);

    sei();
}

int main(void)
{
    init();
   
	for(;;){
		#ifdef WATCHDOG_ON
            wdt_reset();
		#endif

        #ifdef MACHINE_ON
            machine_run();
        #endif

		#ifdef SLEEP_ON
            sleep_mode();
		#endif
	}
}


/**
 * @brief se em debug, fica chaveando os pinos de debugs até o reset do watchdog
 */
ISR(BADISR_vect)
{
    for(;;){
        VERBOSE_MSG_ERROR(usart_send_string("\nFATAL ERROR: BAD ISR."));
        #ifdef WATCHDOG_ON
            VERBOSE_MSG_ERROR(usart_send_string("WAITING FOR WATCHDOG TO RESET...\n"));
        #endif
        #ifdef DEBUG_ON
            DEBUG0;
            DEBUG1;
            _delay_ms(100);
        #endif
    }
}

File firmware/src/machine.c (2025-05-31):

#include "machine.h"

volatile state_machine_t state_machine;
volatile system_flags_t system_flags;
volatile error_flags_t error_flags;
volatile measurements_t measurements;
volatile uint16_t charge_count_error;
volatile uint8_t relay_clk;
volatile uint8_t first_boat_off;
volatile uint8_t machine_clk;
volatile uint8_t machine_clk_divider;
volatile uint8_t total_errors; // Contagem de ERROS
volatile uint8_t reset_clk;
volatile uint8_t led_clk_div;
volatile uint16_t print_clk_div;

/**
 * @brief
 */
void machine_init(void) {
  clr_bit(PRR, PRTIM2); // Activates clock

  // MODE 2 -> CTC with TOP on OCR1
  TCCR2A = (1 << WGM21) | (0 << WGM20)      // mode 2
           | (0 << COM2B1) | (0 << COM2B0)  // do nothing
           | (0 << COM2A1) | (0 << COM2A0); // do nothing

  TCCR2B =
#if MACHINE_TIMER_PRESCALER == 1
      (0 << CS22) | (0 << CS21) | (1 << CS20) // Prescaler N=1
#elif MACHINE_TIMER_PRESCALER == 8
      (0 << CS22) | (1 << CS21) | (0 << CS20) // Prescaler N=8
#elif MACHINE_TIMER_PRESCALER == 32
      (0 << CS22) | (1 << CS21) | (1 << CS20) // Prescaler N=32
#elif MACHINE_TIMER_PRESCALER == 64
      (1 << CS22) | (0 << CS21) | (0 << CS20) // Prescaler N=64
#elif MACHINE_TIMER_PRESCALER == 128
      (1 << CS22) | (0 << CS21) | (1 << CS20) // Prescaler N=128
#elif MACHINE_TIMER_PRESCALER == 256
      (1 << CS22) | (1 << CS21) | (0 << CS20) // Prescaler N=256
#elif MACHINE_TIMER_PRESCALER == 1024
      (1 << CS22) | (1 << CS21) | (1 << CS20) // Prescaler N=1024
#else
      0
#endif
      | (0 << WGM22); // mode 2

  OCR2A = MACHINE_TIMER_TOP; // OCR2A = TOP = fcpu/(N*2*f) -1

  TIMSK2 |= (1 << OCIE2A); // Activates interruption

  set_machine_initial_state();
  set_state_initializing();
}

/**
 * @brief set machine initial state
 */
inline void set_machine_initial_state(void) {
  error_flags.all = 0;
  relay_clk = machine_clk = machine_clk_divider = led_clk_div = 0;
}

/**
 * @brief set error state
 */
inline void set_state_error(void) {
  VERBOSE_MSG_MACHINE(usart_send_string("\n>>>STATE ERROR\n"));
  state_machine = STATE_ERROR;
}

/**
 * @brief set initializing state
 */
inline void set_state_initializing(void) {
  VERBOSE_MSG_MACHINE(usart_send_string("\n>>>INITIALIZING STATE\n"));
  state_machine = STATE_INITIALIZING;
}

/**
 * @brief set idle state
 */
inline void set_state_idle(void) {
  VERBOSE_MSG_MACHINE(usart_send_string("\n>>>IDLE STATE\n"));
  state_machine = STATE_IDLE;
  relay_clk = 0;
  charge_count_error = 0;
}

/**
 * @brief set running state
 */
inline void set_state_running(void) {
  VERBOSE_MSG_MACHINE(usart_send_string("\n>>>RUNNING STATE\n"));
  state_machine = STATE_RUNNING;
  relay_clk = 0;
}

/**
 * @brief set reset state
 */
inline void set_state_reset(void) {
  VERBOSE_MSG_MACHINE(usart_send_string("\n>>>RESET STATE\n"));
  state_machine = STATE_RESET;
  error_flags.no_charge = 0;
}

inline void set_state_waiting_reset(void) {
  VERBOSE_MSG_MACHINE(usart_send_string("\n>>>WAITING RESET STATE\n"));
  state_machine = STATE_WAITING_RESET;
}

/**
 * @breif prints the configurations and definitions
 */
inline void print_configurations(void) {
  VERBOSE_MSG_MACHINE(usart_send_string("CONFIGURATIONS:\n"));

  VERBOSE_MSG_MACHINE(usart_send_string("\nadc_f: "));
  VERBOSE_MSG_MACHINE(usart_send_uint16(ADC_FREQUENCY));
  VERBOSE_MSG_MACHINE(usart_send_char(','));
  VERBOSE_MSG_MACHINE(usart_send_uint16(ADC_AVG_SIZE_10));
  VERBOSE_MSG_MACHINE(usart_send_string("\nmachine_f: "));
  VERBOSE_MSG_MACHINE(usart_send_uint16(MACHINE_FREQUENCY));

  VERBOSE_MSG_MACHINE(usart_send_char('\n'));
}

/**
 * @brief prints the system flags
 */
inline void print_system_flags(void) {
  usart_send_string("\tB_on: ");
  usart_send_uint16(system_flags.boat_on);
  usart_send_string(" B_charg: ");
  usart_send_uint16(system_flags.boat_charging);
  usart_send_string(" B_running ");
  usart_send_uint16(system_flags.boat_running);
}

/**
 * @brief prints the error flags
 */

inline void print_error_flags(void) {
  VERBOSE_MSG_MACHINE(usart_send_string("\nError no canbus: "));
  VERBOSE_MSG_MACHINE(usart_send_uint16(error_flags.no_canbus));
  VERBOSE_MSG_MACHINE(usart_send_string(" Error no charge: "));
  VERBOSE_MSG_MACHINE(usart_send_uint16(error_flags.no_charge));
}

/**
 * @brief Checks if the system is OK to run
 */

void pulse_mainrelay_on(void) {
  clr_mainrelay_off(); // having shure to not set both coils at the same time
  _delay_ms(10);

  // apply a pulse of 250ms
  set_mainrelay_on();
  _delay_ms(100);
  clr_mainrelay_on();
}

/**
 * @brief turns off the mainrealy (a laching relay) by using a pulse of 250ms
 */
void pulse_mainrelay_off(void) {
  clr_chargerelay();

  clr_mainrelay_on(); // having shure to not set both coils at the same time
  _delay_ms(10);

  // apply a pulse of 250ms
  set_mainrelay_off();
  _delay_ms(100);
  clr_mainrelay_off();
}

/*
 * @
 * @breif turns the boat on, slowly charging the caps before activate the
 * main relay
 */

void turn_boat_on(void) {
#ifdef VERBOSE_ON_RELAY
  VERBOSE_MSG_MACHINE(usart_send_string("Turning boat on"));
#endif
  pulse_mainrelay_on();
  _delay_ms(200);
  clr_chargerelay();
}

/*
b2rief turns the boat off.
 */
void turn_boat_off(void) {
#ifdef VERBOSE_ON_RELAY
  VERBOSE_MSG_MACHINE(usart_send_string("Turning boat off"));
#endif

  clr_chargerelay();
  _delay_ms(50);
  pulse_mainrelay_off();
  _delay_ms(50);
  pulse_mainrelay_off();
  _delay_ms(50);
  pulse_mainrelay_off();
  _delay_ms(50);
}
void turn_charge_boat_on(void) {
  set_chargerelay();
  system_flags.boat_charging = 1;
}

void turn_charge_boat_off(void) {
  clr_chargerelay();
  system_flags.boat_charging = 0;
}

/**
 * @brief read and checks current levels
 */
inline void read_and_check_adcs(void) {
#ifdef ADC_ON
  measurements.cap_voltage =
      MA_CAP_VOLTAGE; //* CONVERSION_BATTERY_VOLTAGE_VALUE;
  measurements.bat_voltage =
      MA_BATTERY_VOLTAGE; //* CONVERSION_BATTERY_VOLTAGE_VALUE;

  switch (state_machine) {
  case STATE_INITIALIZING:
    // check_battery_voltage();

    break;
  case STATE_IDLE:
    // check_battery_voltage();

    break;
  case STATE_RUNNING:
    // check_battery_voltage();

    break;
  default:
    break;
  }
#endif
}

inline void task_initializing(void) {
#ifdef LED_ON
  set_led(LED1);
  set_led(LED2);
#endif

#ifdef RELAY_TEST_MODE
  VERBOSE_MSG_INIT(
      usart_send_string("System initializing in RELAY_TEST_MODE.\n"));
#endif

  system_flags.boat_on = 0;
  turn_boat_off();

  set_machine_initial_state();

  VERBOSE_MSG_INIT(usart_send_string("System initialized without errors.\n"));
  set_state_idle();
}

/**
 * @brief waits for commands while checking the system
 */
inline void task_idle(void) {

// This module in particular has delays on idle state
// So there is no idle_led_clk_div
#ifdef LED_ON
  //   if (led_clk_div++ >= 1) {
  cpl_led(LED1);
  set_led(LED2);
  // led_clk_div = 0;
//   }
#endif
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

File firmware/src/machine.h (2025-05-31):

/**
 * @file machine.h
 *
 * @defgroup MACHINE State Machine Module
 *
 * @brief Implements the main state machine of the system.
 *
 */

#ifndef MACHINE_H
#define MACHINE_H 

#include <avr/io.h>
#include <avr/wdt.h>
#include <avr/interrupt.h>
#include <util/delay.h>

#include "conf.h"

#define MA_CAP_VOLTAGE      ma_adc0()
#define MA_BATTERY_VOLTAGE      ma_adc1()

// LED CONSTANTS
#define IDLE_LED_TIME           1 // half a period...time that the LED stays on
#define IDLE_LED_CLK_DIV        IDLE_LED_TIME * 2 * MACHINE_FREQUENCY //  
#define ATTENTION_LED_TIME      0.1 // half a period...time that the LED stays on
#define ATTENTION_CLK_DIV       ATTENTION_LED_TIME * 2 * MACHINE_FREQUENCY //  

// PRINT INFOS CONSTANTS
#define PRINT_INFOS_TIME        0.2 // seconds 
#define PRINT_INFOS_CLK_DIV     PRINT_INFOS_TIME * 2 * MACHINE_FREQUENCY

#ifdef ADC_ON
#include "adc.h"
#endif
#ifdef USART_ON
#include "usart.h"
#endif
#include "dbg_vrb.h"
#ifdef CAN_ON
#include "can.h"
#include "can_app.h"
extern const uint8_t can_filter[];
#endif

typedef enum state_machine{
    STATE_INITIALIZING,
    STATE_IDLE,
    STATE_RUNNING,
    STATE_ERROR,
    STATE_RESET,
    STATE_WAITING_RESET,
} state_machine_t;

typedef union system_flags{
    struct{
        uint8_t     boat_on        :1;
        uint8_t     boat_charging  :1; 
        uint8_t     boat_running :1;
    };
    uint8_t   all__;
} system_flags_t;

typedef union error_flags{
    struct{
        uint8_t     no_canbus     :1;
        uint8_t     no_charge     :1;
    };
    uint8_t   all;
}error_flags_t;

typedef struct measurements{
    uint16_t    cap_voltage;       // period maximum value of ADC1
    uint16_t    bat_voltage;       // period maximum value of ADC1
}measurements_t;


// machine checks
void check_buffers(void);
void read_and_check_adcs(void);

// debug functions
void print_configurations(void);
void print_system_flags(void);
void print_error_flags(void);
void print_infos(void);

// machine tasks
void task_initializing(void);
void task_idle(void);
void task_running(void);
void task_error(void);
void task_reset(void);
void task_waiting_reset(void);

// the machine itself
void set_machine_initial_state(void);
void machine_init(void);
void machine_run(void);
void set_state_error(void);
void set_state_initializing(void);
void set_state_idle(void);
void set_state_running(void);
void set_state_reset(void);
void set_state_waiting_reset(void);

//relay functions
void pulse_mainrelay_on(void);
void pulse_mainrelay_off(void);
void turn_boat_on(void);
void turn_boat_off(void);
void turn_charge_boat_on(void);
void turn_charge_boat_off(void);

// machine variables
extern volatile state_machine_t state_machine;
extern volatile system_flags_t system_flags;
extern volatile error_flags_t error_flags;
extern volatile measurements_t measurements;
extern volatile uint16_t charge_count_error;
extern volatile uint8_t relay_clk;
extern volatile uint8_t first_boat_off;
extern volatile uint8_t machine_clk;
extern volatile uint8_t machine_clk_divider;
extern volatile uint8_t total_errors;           // Contagem de ERROS
extern volatile uint8_t reset_clk;

// other variables
extern volatile uint8_t led_clk_div;
extern volatile uint16_t print_clk_div;

#endif /* ifndef MACHINE_H */

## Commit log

2019-03-28 NÃO FINALIZADA Primeira versão do esquematico Foi reciclado o modulo atmega e can do MSC19
    [CAN_ON_OFF.sch, Charger.sch, analog.sch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]
2019-03-29 Primeira versão do esquematico finalizada Falta DRC
    [CAN_ON_OFF.sch, Charger.sch, atmega328p.sch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]
2019-03-31 O fusivel do sistema foi movido pro GND
    [Charger.sch, analog.sch, main.sch]
2019-03-31 Abstração do esquemático modificada para separar as duas placas e mostrar a conexão entre elas na folha principal
    [CAN_ON_OFF.sch, Charger.sch, analog.sch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]
2019-03-31 TO-DO List criada na folha principal
    [Charger.sch, analog.sch, atmega328p.sch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]
2019-03-31 Alimentação de 12V criada no Charger, que recebe 18V do Controller
    [Charger.sch, controller.sch, main.sch]
2019-03-31 Folha modificada para A3
    [Charger.sch]
2019-03-31 CAN CTRL_D / CAN_ON_OFF removidos.
    [Charger.sch, analog.sch, atmega328p.sch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]
2019-03-31 Novos capacitores anotados
    [Charger.sch]
2019-03-31 Analog passado para o Charger
    [Charger.sch, analog.sch, atmega328p.sch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]
2019-04-02 Esquematico primeira versão Erro de referencia dos componentes na PCB com os do Esquematico solucionados
    Pontos de teste adicionados
    Alimentar o analog com +12V
    Adicionar Snubber para os reles
    [Charger.sch, analog.sch, atmega328p.sch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]
2019-04-02 Generic layout and relay driver
    [Charger.sch, main.kicad_pcb]
2019-04-04 Copper bar fixation
    [12V.sch, Charger.sch, _saved_Charger.sch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]
2019-04-04 Layout and Relay footprint
    [Charger.sch, _saved_Charger.sch, main.kicad_pcb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]
2019-04-05 Ampop layout not finished
    [Charger.sch, analog.sch, main.kicad_pcb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]
2019-04-06 Circuito ampop incompleto
    [analog.sch, atmega328p.sch, canbus.sch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]
2019-04-14 Layout retrabalhado. Não finalizado.
    [12V.sch, Charger.sch, analog.sch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]
2019-04-15 Signals tracks routed
    [main.kicad_pcb]
2019-04-15 First version PCB
    [Charger.sch, _saved_Charger.sch, analog.sch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]
2019-04-19 Small updates
    [main.kicad_pcb, main_bk.kicad_pcb, main_panel.kicad_pcb]
2019-04-21 Connector to join the modules, were centrailized Compacted Atmega PCB
    [12V.sch, Charger.sch, _saved_Charger.sch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]
2019-04-21 Files organization
    [rj45.step]
2019-04-21 3D fixation
    [Assem1.SLDASM, Assem85.SLDASM, COMPOUND.sldprt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]
2019-04-21 small update
    [_saved_atmega328p.sch, atmega328p.sch, main.kicad_pcb]
2019-05-03 Ampop gain error
    [12V.sch, Charger.sch, analog.sch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]
2019-05-16 Charging logic finalized
    time and voltage verification before turn boat on ,when is charging
    if is under-voltage enter in error state
    [machine.c, machine.h]
2019-05-18 Under_voltage error after charge fixed
    Quando testava se depois de carregar o capacitor, ele estava carregado, o modulo comparava entre uma constante e a tensão do capacitor.
    Essa logica tinha um erro quando a tensão da bateria era menor que a
    maxima, pois o capacitor nunca chegava na constante.
    Para solucionar isso o codigo compara se a tensão do capacitor esta uma percentagem definida abaixo da bateria
    [adc.c, conf.h, machine.c]
2019-05-18 Declared functions and variables for the wait for reset tasK
    [conf.h, machine.c, machine.h]
2019-05-20 waiting for reset task working!!!
    In function machine_run, in switch of state_machine was missing a
    "break" in case STATE_WAITING_RESET
    In the end of error_task function was calling the set_state_initializing
    function ignoring all states called before that,then set_state_initializing was moved to
    the begining of error task function.
    [conf.h, machine.c]
2020-01-19 reorganized, 3d exported
    [12V.sch, Assem1.SLDASM, Assem85.SLDASM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]
2022-03-19 Use extern modifier to fix duplicated variables being defined on newer GCC
    [adc.c, can_app.c, machine.c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]
2022-03-19 can_app: Fix switch fall through.
    [can_app.c]
2025-05-31 change adc logic to circular buffer
2025-05-31 main does not touch LED
2025-05-31 Better macros, using new adc logic
2025-05-31 using new adc logic - NO max min implementation yet
2025-05-31 Linearized adc channels
2025-06-11 standard code - comment relay_test_mode
